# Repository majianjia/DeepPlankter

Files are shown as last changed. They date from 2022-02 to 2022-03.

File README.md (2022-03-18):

# DeepPlankter

An autonomous wave and wind propelled drone boat.

It uses free energy in the surrounding environment to sail for a very long distance. It relies on in-air free-rotate wing and the underwater wings to provide propulsion and solar panels to power the onboard electronics.  

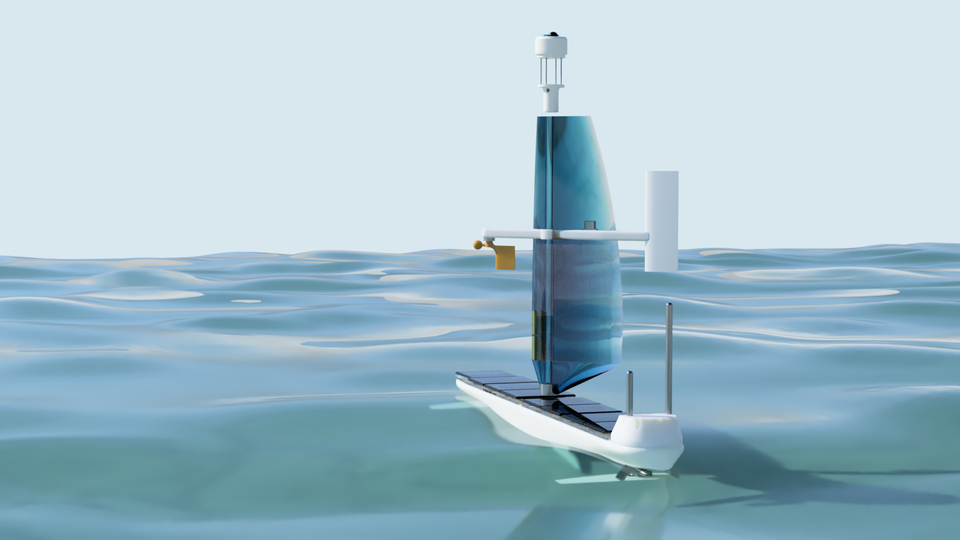
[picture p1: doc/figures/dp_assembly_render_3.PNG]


This repo hosts the main design files (PCB, mechanical parts and development logs) of the DeepPlankter project, excluding the boat controller firmware and communication method.

- The source code of **navigation controller firmware** will be hosted in its own [repo (Not yet public)]() 

- **Communication protocols and the remote control App/Website** are **NOT** opensourced because of safety reasons.

### Building log

1. [Hull building](doc/hull.md)

2. [Underwater Wings](doc/underwater_wing.md)

3. [Navigation algorithm](doc/navigation.md)

4. [Science Payload](doc/science_payload.md)

### Experiment log

1. [First motor powered experiment](doc/exp1_pond.md)

2. [Second motor powered experiment](doc/exp2_pond.md)

# 3D designs

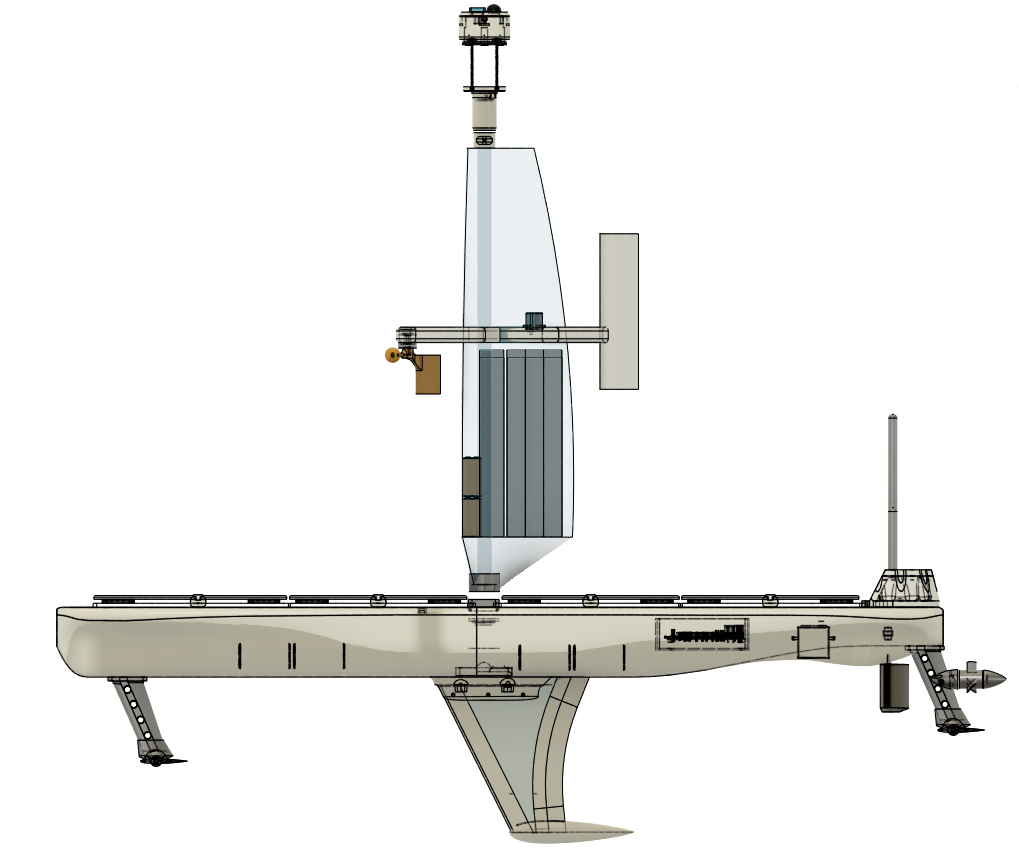
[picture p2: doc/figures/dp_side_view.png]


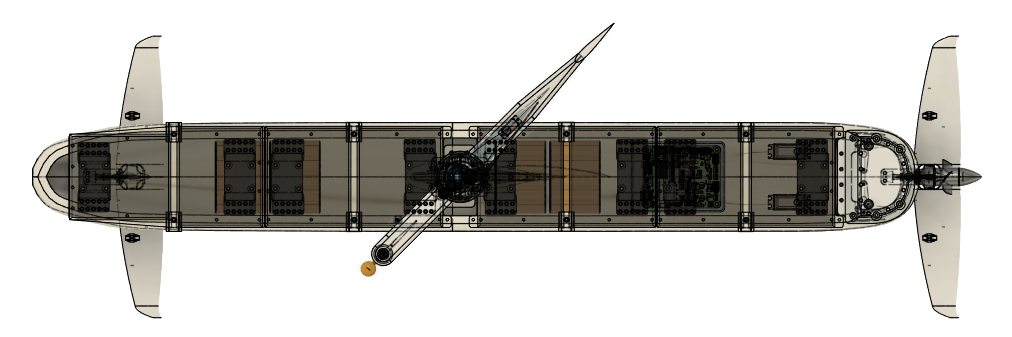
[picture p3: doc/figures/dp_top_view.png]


# Hardware

PCB file can be found in [PCB](PCB) folder. 

**The boat controller:**

- Dimension: 80 x 100 mm
- MCU: STM32H7A3ZI, 280MHz, 1MB SRAM, 2MB Flash. 
- NorFlash
- RTC

**Sensors:**

- IMU: BMI088
- e-compass: HMC5883L
- Environment sensor: BME280 (humidity, atmospheric pressure, temperature)

**Power supplies:**

- DC/DC LMR33640, 5.1V, 4A (max) x 3 controlled channels.
- DC/DC LMR33640, 3.3V, 4A (max) x 2 controlled channels.
- 2 battery connectors 
- 2 charging connectors. 

**Power connector functions and monitoring**

| Connector | Ctrl. Switched | Voltage gauge | Current gauge | Comments |
| --- | --- | --- | --- | --- |
| 3.3V (CH1, CH2) | yes | | | |
| 5V (CH1, CH2, CH3) | yes | | | |
| BAT (CH1, CH2) | *yes | yes | yes | Base on ideal diode controller. |
| Charge (CH1, CH2)  | | *note | yes | Voltage = BAT |
| ESC power | yes | *note | yes | Voltage = BAT |
| Servo (CH1, CH2) | yes | *note | yes | Voltage = BAT |
| Servo (CH3) | | *note | | Voltage = BAT |

**Extension IOs:**

- 2 x 2P NTC (for each battery)
- 1 x 2P ADC
- 1 x 2P External LED (Flash light)
- 1 x 2P External Buzzer
- 3 x 6P UART (marked TELE1, TELE2, main GPS)
- 2 x 4P UART
- 2 x 8P SPI (MISO, MOSI, SCK, CS1, CS2, IO)
- 2 x 4P I2C (same PHY)
- 1 x 4P FDCAN
- 1 x USBD
- 1 x 24P FPC DCMI camera interface (for OV2640)
- 1 x 8P FPC and 2x4 rows debugging port (SWD + UART)
- 1 x SDCard slot (SDIO)

## Battery, solar panels and MPPT chargers

- Battery 1: 18650 1500mAh 2S 9P
- Battery 2: 18650 1500mAh 2S 9P
- Panel set 1: 12V 160mA 4P 
- Panel set 2: 12V 160mA 4P 
- MPPT charger: BQ24650 model x 2
- 2S over current protector and balance x 2
- NTC x 2

The power of the whole boat is purely supplied by solar panels. We need to ensure the main controller never run out of power. The power distribution is managed by the main controller board. 8 panels are grouped into 2 set with 4 panels in each set. Each set of panels charge one battery through an independent MPPT charger and is balanced by an independent protect board. The power from the 2 batteries finally merges to a power rail through 2 ideal diode circuits. Then the power can be distributed by the main controller board.

The voltage and current of each charging circuit and battery are monitored.

### Energy estimation

Each panel is rated 12V@160mA. In a sunny April day noontime, the maximum current measured is 10.5V@120mA when laying flat (simulate the angle on the boat).

So the peak power is around 1.25W for each panel. 8 of them can generate 10W.

But there are efficiency drops due to DC/DC converter and the battery charging efficiency. We assume it is around 0.8, so the peak power to charge the battery is 8W.

The peak power multiple by the term, "peak sun hours", is the energy that generated per day.  
For example,  per [this blog](https://www.pveducation.org/pvcdrom/properties-of-sunlight/average-solar-radiation#), in UK summertime, the peak sum hour is 5 hours, while in the winter, the number drops to 0.5 hours, so the power generated per day is around 40wh to 4wh.

> The average daily solar insolation in units of kWh/m2 per day  is sometimes referred to as "peak sun hours". The term "peak sun hours"  refers to the solar insolation which a particular location would receive if the sun were shining at its maximum value for a certain number of  hours. 

Sailing during the winter is definitely a nightmare for the boat no matter how big the battery is, it will be drained out very soon if we don't cut off the power to every module or put them into sleep mode.

We have 2 battery sets, each can store around 100Wh. It needs 5 sunny days to fully charge.

Both batteries together can supply a 1W consumption (3.3V 300mA) for a good week until the next sunny day. Or 0.2W (3.3V 60mA)for a month.

# Contact

Jianjia Ma 
`majianjia(-at-)live.com`

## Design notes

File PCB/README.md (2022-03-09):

# Hardware Defect

- Console UART debug port tx/rx swapped. 
- Camera LDO 2.8v and 1.2v switched. 
- R90 removed

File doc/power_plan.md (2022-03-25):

# Power plan

The the power all power plan on the boat is shown below.

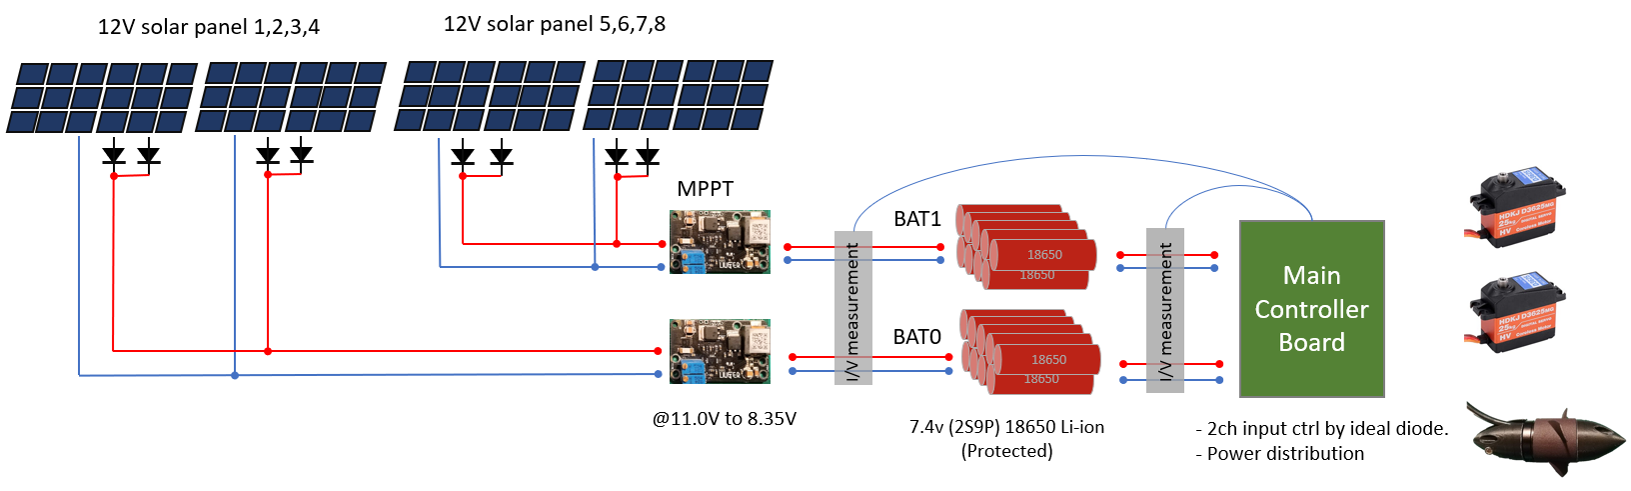
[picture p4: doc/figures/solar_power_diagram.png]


This is a simplified diagram that doesn't include power switches, battery protection circuits, temperature sensing and some other current sensing. 

## Solar panels

Our panels are laid flat on the deck so the sun angle is very important for the test because the angle of light affect the effective area on the panels. 

The panel has rated 12V at 160mA under 1000W/m^2 (this number is about the direct sunlight on the ground). According to my previous measurement, each panel measured open-circuit voltage at 13.7V and short-circuit current at ~150mA. 

A solar panel power test was done on 17 March.

On 17 March 2022, the maximum sun angle is 40 degrees in Southampton UK. If we only consider the power is produced by the direct sunlight but not scattering light (discuss later), the panels generate 76% power of its right angle sunlight theoretically.

As you can see from the power plan diagram, we have 2 sets of panels, 4 panels per set. Each rated 1.8 W according to their official data. So the maximum output for use should be 1.8 x 76% = 1.35W. Below is the measured power from the 2 sets of panels. 

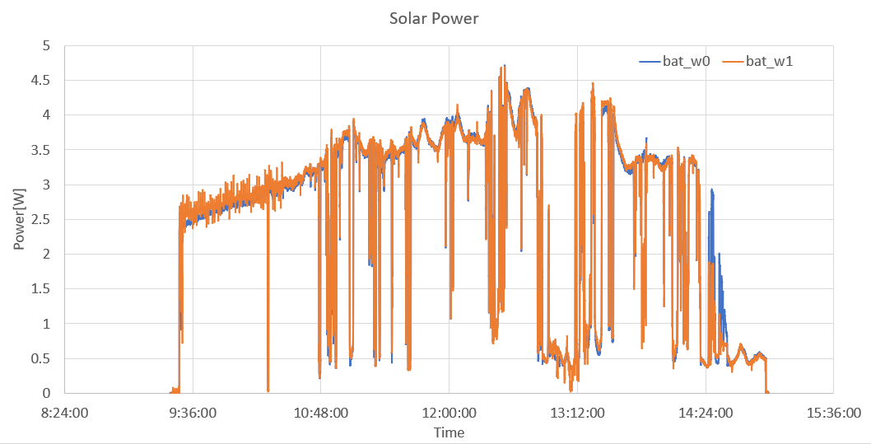
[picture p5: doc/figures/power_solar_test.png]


There is some noticeable information from the graph. 

- Both sets of panels generate very similar output.

- At peak sun degree (12 o'clock, 40 deg height), each set of panel generate 4W power, (1W per panel), this number is lower than our calculation of 1.35 W. There are multiple reasons for it, 1) the series connected Schottky diodes consume power. 2) the MPPT voltage is set lower than the optimal voltage (discuss later.) 

- The peak power isn't the clear sky. If you see from 9:30 to 10:30 when the sky is crystal clear, the power output is steadily increased, but starts around 10:48, a higher peak power is received but together with some drops. The drops were due to cloud shade. The increased peak power is because the cloud is scattering sunlight which leads to more energy radiating on the panels. This is only my thought to explain this counterintuitive phenomenon. Whether the at a certain density of cloud will generate more energy than clear sky, I don't know. 

- In total, during the 5 hours experiment, the 2 sets of panels generate 24Wh energy, if we expend the time before 9:00 and after 15:00, I estimate it can generate 36Wh. I think this result is very promising. One of these partially cloudy days allows the boat to work 2 to 3 days. I am sure the boat can sustain most of the year and bad weather. 

What this number also means is that the sunlight can drive the boat in the daytime infinitely with 20% of the thruster throttle. In the second motor-driven test, at 20% throttle, the motor takes around 6W power while it can push the boat at a speed of 1.5 knots.   

Below photo was took at 10:26. 

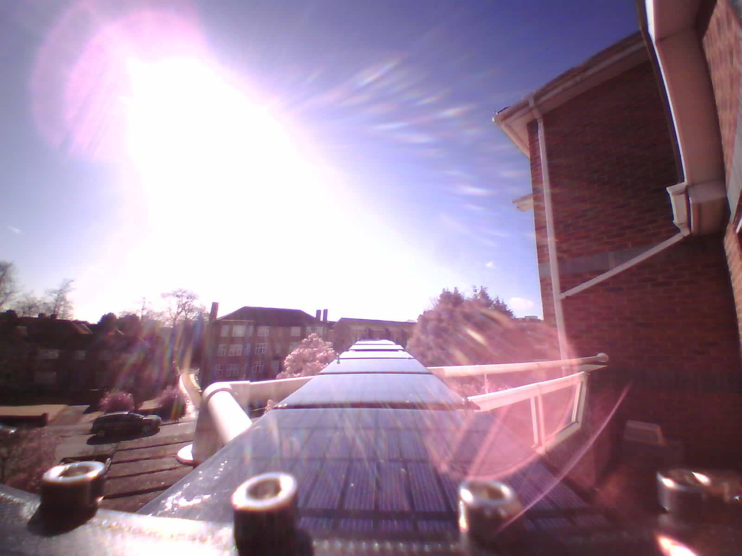
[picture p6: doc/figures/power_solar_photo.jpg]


## MPPT voltage and charge voltage

The MPPT module has 4A maximum current but apparently we won't use that much. The nominal voltage for the solar panel is 12V (24 small cells in series), but because we are using parallel connections, a Schottky diode is needed for each panels, in case of uneven lighting causing too much reverse current (turning the shaded panel into LED). Because the voltage drop of the diode, the MPPT point should be set lower. Per the datasheet of the diode I used, the voltage drop at 100mA is around 0.4V. So the MPPT point should be tuned at 11.6V. 

However, if you see the graph carefully, you will notice that the MPPT
voltage is in fact set to 11V which is lower than our calculation above. My
consideration is

- When the lighting is low, the solar panel's MPPT voltage is also reduced. If we still use the higher voltage, we will get very little power out. This is very important because we want the panel to produce power in bad weather more than on sunny days. A lower MPPT voltage decreases the power output on sunny day a bit but will ensure the panels work in darker lighting conditions.

- Besides lighting, a lower voltage can ensure all panels has space to generate current when they are not exactly the same. For example, some of them might be degraded differently during a time or they came with manufacturing defects. Result in cannot reach the higher MPPT voltage.

- Since we have a fixed MPPT voltage setting, a lower voltage will ensure us a larger safety margin.

To be continued..

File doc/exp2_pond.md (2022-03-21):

# Second motor powered experiment

After the first experiment, lots of issues were found. Fixing them took quite a lot of time but finally was all solved. .

So I decided to take another motor propelled experiment to test the rudder effectiveness and the waypoint mission. 

Overall, the experiment went well. 

- rudder effectiveness improved by increasing the angle limitation and extending the length. 

- There is still a problem with LORA communication. 

- There is only one water leaking issue found on the bow deck due to a unscrew bolt. 

- Waypoint planning seems effective, the boat can drive itself toward the waypoint and path direction. Although the turning radius is still quite large. 

- Camera exposure is now working correctly, however, there were some issues with the wire connection. All images taken during the experiment are broken, cannot be fixed. It's a pity. 

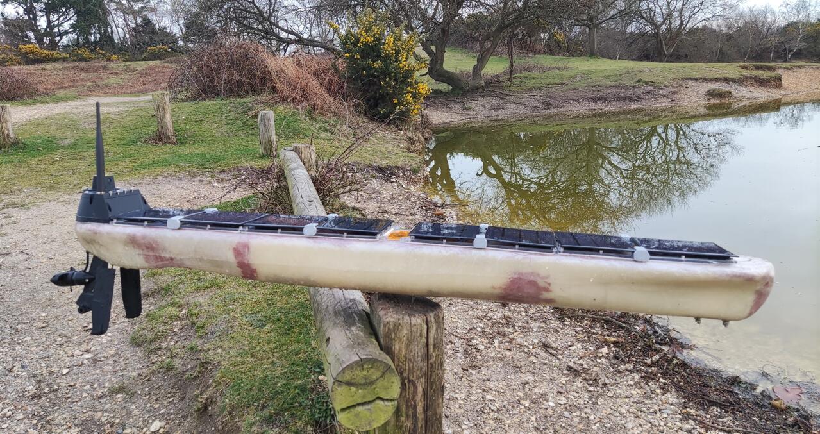
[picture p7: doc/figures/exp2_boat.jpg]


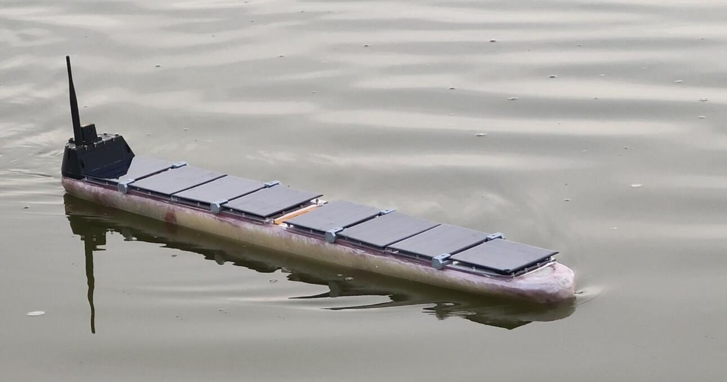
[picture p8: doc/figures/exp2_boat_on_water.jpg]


## Waypoint mission

Thanks to the navigation simulator, I was able to validate my navigation algorithms in the simulated world. See the [navigation development log](navigation.md) for details.

I use the default parameters for the waypoint mission, which is very rough and conservative. however, it did work well. The PID parameters were set to 1, 0, 0. which means every metre of  *cross track error* turns the rudder for 1 degree. No integration and damping components. The pond seems a little bit small for testing the waypoint function but the result is still exciting. 



While we solved the EMI issue, the GNSS can locate the boat pretty well now. 

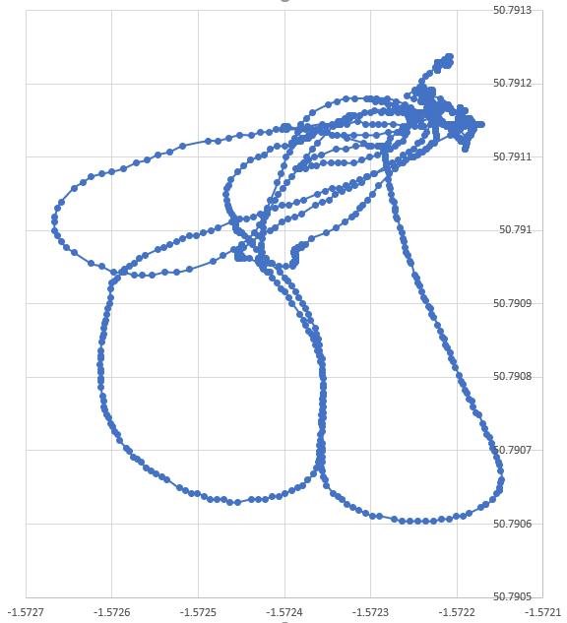
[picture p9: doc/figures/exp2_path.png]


With only 20% of throttle, the boat sails peacefully. 



## Unstable rolling motion

without hydro wings, keel and underwater ballast, the boat is still unstable at high throttle. 

I am not worrying too much about that because when the wing sail is ready, we must install the keel together with the ballast. 

## Minor water leaking

The gaps between the screw and polycarbonate glass are not sealed correctly. When water came up to the deck, it is leaking into the boat. I bought a bag of O ring for sealing the gap, hopefully can fixed this issue. 

The other water leaking source is the screws for the 3D printed solar panel mounts. The bot underneath became loose very easily when some water is leaking in. I would seal them with silicone glue for the future test.

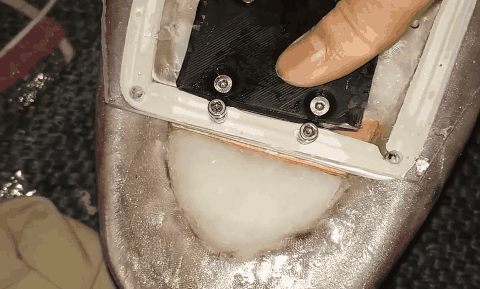
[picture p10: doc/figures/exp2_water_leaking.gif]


## Batteries management issue

- One of the protectors is broken. Looks like the IC is bricked at charge protection. I could not recover from the error state. I replaced the protection board with a working one.

- The motor drain majority of current from one of the battery. Later found this was due to a short under the ideal diode controller.  Fixed. 

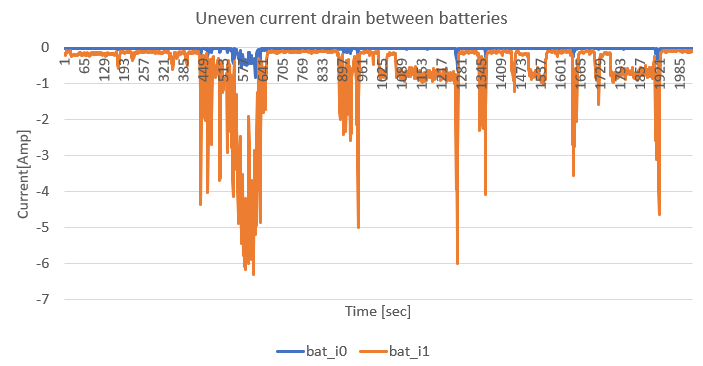
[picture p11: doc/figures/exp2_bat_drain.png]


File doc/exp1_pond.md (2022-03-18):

# First motor powered experiment

Did a experiment at Setley Pond, New Forest this Sunday afternoon 7th March 2022. 

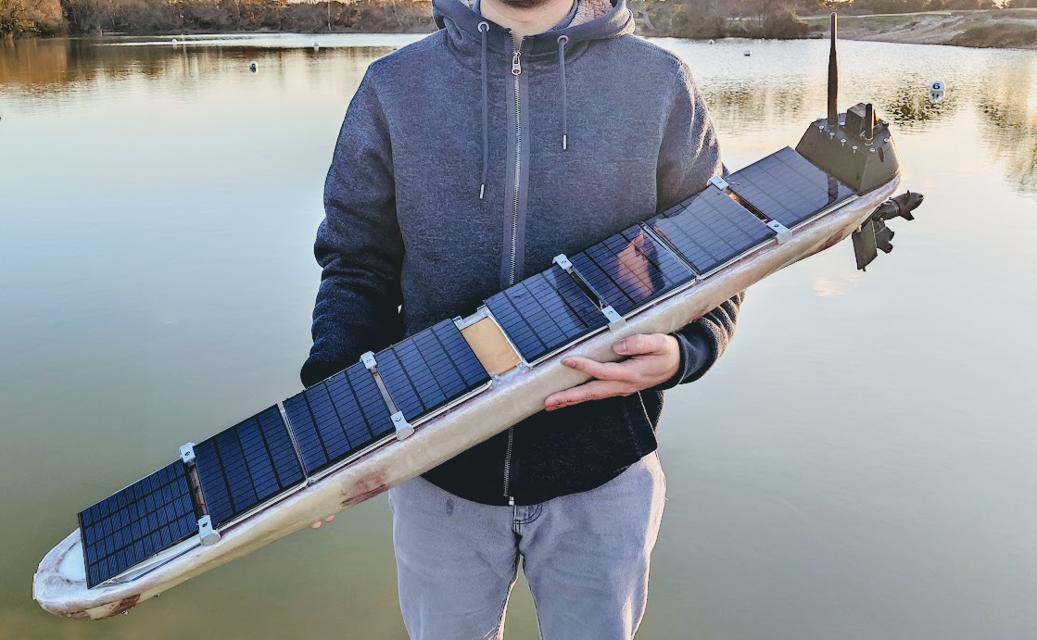
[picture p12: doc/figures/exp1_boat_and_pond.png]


In this experiment, I would test a few different things. Including

- manual control and motor drive.
- underwater wings. (cancelled, due to no wave)
- waypoint mission. (cancelled, due to low rudder effectiveness)

As you expected, this experiment wasn't going well. Fortunately, the boat float and recovered. Also, [data](../experiments/2022-03-06%20dp%20first%20water%20run) are recorded so we have something to analysis.

The motor can really push the quite fast, even the throttle has been limited to 50%. The motor consume around 5 Amp current at 50% throttle. When I pushed the throttle fully from the App (50%), I am quite worry about the boat sinking into the water and become a submarine... Beside the boat was not being able to turn, it is really fun to play with.



Trying to plot the GNSS location in a map, but due to the EMC problem that discuss below, the GNSS can only be located by 4-5 satellites during the trial, the accuracy is pretty low, the path is meaningless. 

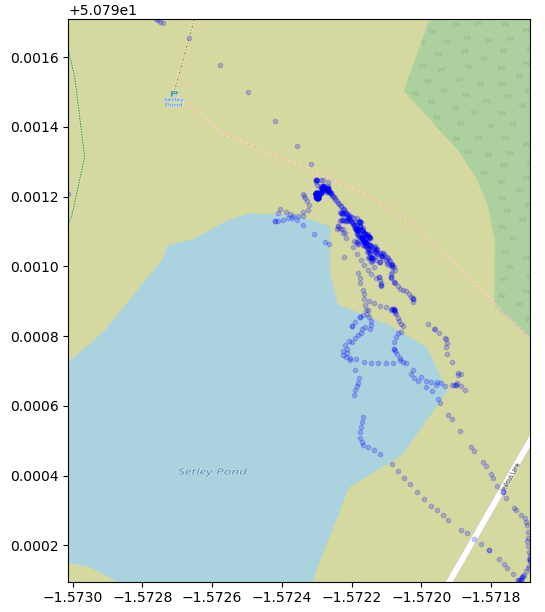
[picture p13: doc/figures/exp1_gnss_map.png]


In the next sessions, I will show the issues that found during the experiment and some of the solutions. 

## Issues

- [EMC problem with antennas](#emc-issue). 

- [Water leaking from unknow source](#water-leaking-issue).

- [Dead servo might due to over voltage](#servo-found-dead).

- [Low rudder effectiveness](#low-rudder-effectiveness). 

- [ESC response too slow](#esc-response-too-slow). 

- [Batteries magnet field affecting magnetometer](#batteries-magnet-field-affecting-magnetometer). 

- [Boat mass centre too high, unstable](#boat-mass-centre-too-high). 

- [Camera data error and image over exposure](#camera-data-error-and-image-over-exposure). 

### EMC issue

At the experiment, all antennas are placed in the bridge at the tail of the boat. 

SIM800C's antenna is placed closed to LoRa's antenna, even in  the same direction. What makes things even worst is they are working at a similar frequency band 800/900M for GSM and 868M for LoRa.  It was ok during home test because the city area has better cellular coverage so the GSM module won't emit too much power. But in the rural, it starts to emit more power so the LoRa is now struggling to send/receive data. 

GPS module also suffered from the GSM module's RF. From the data it recorded, I can see there is only 5 satellites connections when the boat was on the surface of the water, where the signal is weaker. But when I recovered the boat and raised the boat to my car's boot, then it can see 10+ satellites.

The potential solution is to move the GSM module and its antenna to the bow of the boat. 

For the Iridium, I think it will be ok to stay at the tail bridge because it won't be activated too much. 

The GSM module cannot be placed at the mat because the QingStation uses BME280 for pressure and humidity measurement, which is RF sensitive. 

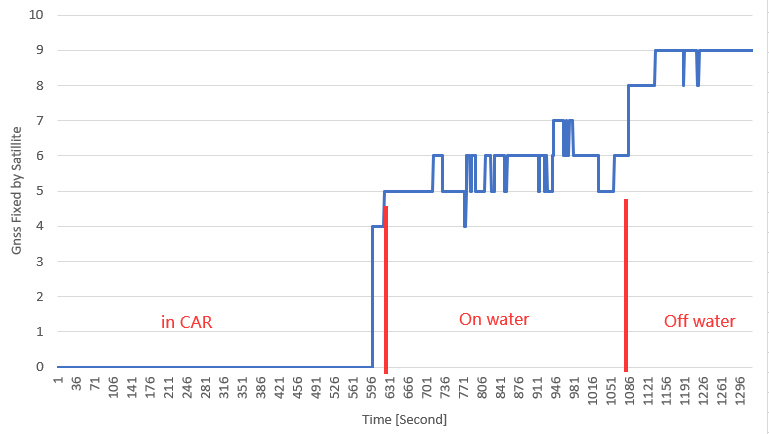
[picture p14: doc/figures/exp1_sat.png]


### Water leaking issue

There was a half cup of water found after I returned home. It is fortunate that I remove the battery from the controller board before I set off. I had to dry out the batteries because they are wet. 

I think it might come from some screw holes that I did not put a screw in. Hopefully, I can fix that later. 

### Servo found dead

One of the servo, servo 1, left rudder, was found dead just before deploying the boat. I supply direct battery voltage to the servo, which is 8V currently, the Servo's working voltage was rated at 4.8 to 7.2V. Looks like it burned out the servo. I disassembled the dead servo but couldn't find a burning spot on the controlling PCB. The reason of the failure remains unclear. 

I order a few mini-360 step-down DC/DC boards to lower the voltage and a new servo to replace the dead one. I would set the voltage to 5.5V. The recorded peak working current for these servos is less than 1A. I believe the small DCDC board can handle the servo's current.

### Low rudder effectiveness

This issue is partially related to the dead servo, but also the length of the rudder is underestimated. I did try to build an extended rudder that can stick on the existing rudder which I brought long time ago designed for RC boat. 

The range of servo is set to +-30 degree, which seems too narrow. It is now increased to +-60. The actual angle that the rudder can turn is smaller than servo angle. 

With only one working rudder, the boat can barely turn at high speed. I think that is because the motor was placed far behind the rudder.  The blue highlighted part is the new extension that will be added to the rudder. 

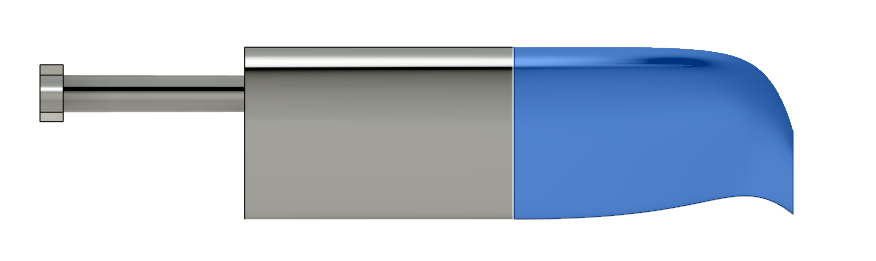
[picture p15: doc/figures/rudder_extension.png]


### ESC response too slow

I added a smooth throttle response in the software to eliminate the immediate change direction of the motor. But the value is too large. Adding some signalling delay, the boat feels like out of control many times, did not response for 5 seconds, while I did hear the servo is still responding to my command. Easy fixed issue. 

### Batteries magnet field affecting magnetometer

Fixed by moving the battery forward.. 10 cm away of controller box.

### Boat mass centre too high

Due to the heavy solar panels, the decks and the screws to fixed the decks, the mass centre were lifted too high, resulting in unstable roll motions. Even the propeller rotation cause 20 degrees rolling. 

I brought 1.8kg lead ingots for ballast, each 450g. I will attach 900g to the bottom of the boat hull. When the keel is ready, I will then move them to the bottom of the keel for the best ballast. 

### Camera data error and image over exposure

Due to the low-frequency clock, 2.5MHz, while the OV2640 require at least 6MHz. The OV2640 seems cannot automatically adjust the exposure time (not short enough). The signal length is too long, about 30CM, any clock higher than 2.5M will not work. It is already producing quite a lot of byte error at 2.5M, see images below. 

I will turn the software while keeping the frequency low. If there is no way to configure it, I will try to attach a grey scale filter on the lens to lower the lights. 

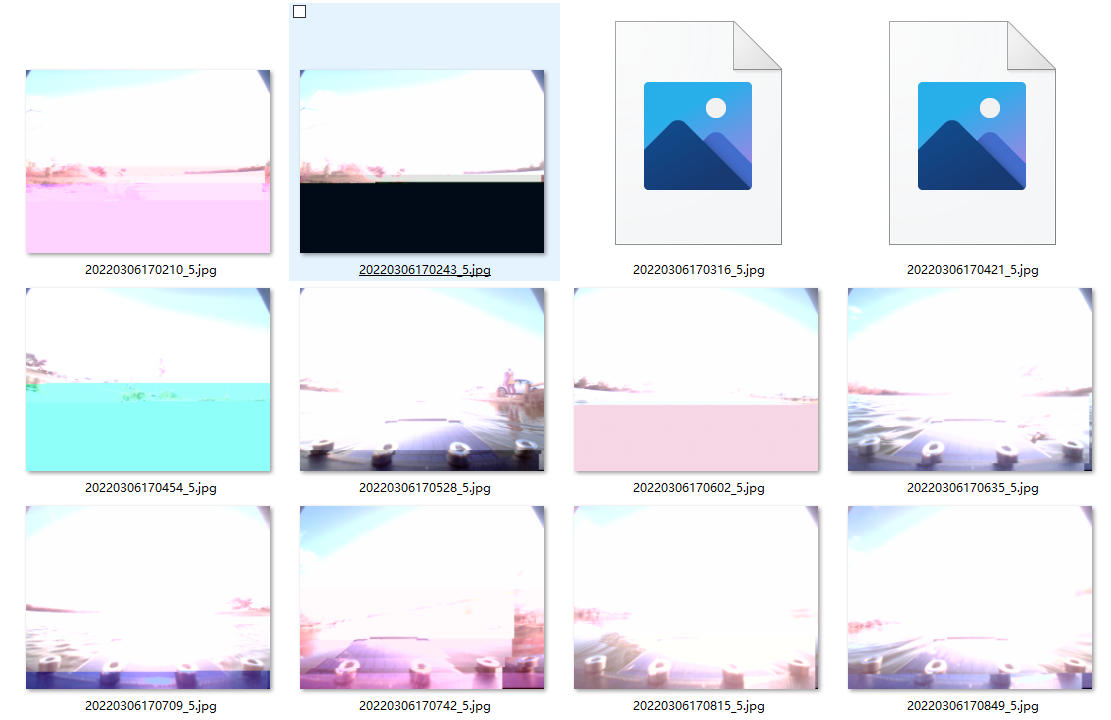
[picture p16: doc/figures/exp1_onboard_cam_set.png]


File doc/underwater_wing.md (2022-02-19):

# Underwater Wings

The underwater wings are to convert the vertical motion (wave) of the hull to small forward propulsion. So the boat can sail forward without the need for energy.

I was planned to build the wing core from wood pieces. Cut the shape, then sand it down to streamline. But later I decided to let the 3d printer build the core. There are some issues with 3d printed parts.

- The PLA materials that 3d printer used might degrade in salt water ( which is not, later confirmed by research paper. )

- PLA can crack easily. 

- If we reinforce with glassfibre and epoxy, the epoxy has difficulty to glue on epoxy. 

To solve the second problem, we use a tough PLA to print the main part. For the third problem, I planned to use rough sand paper to sand it down and leave more scratches for the epoxy to grab on. 

I didn't use a standard airfoil on the underwater wing but built from my own experience from RC planes. The airfoil is symmetric so it should perform the same for both upward and downward directions.  It also has a small wing tip to lower the drag from induced drag (not sure whether this is useful but looks cool. )

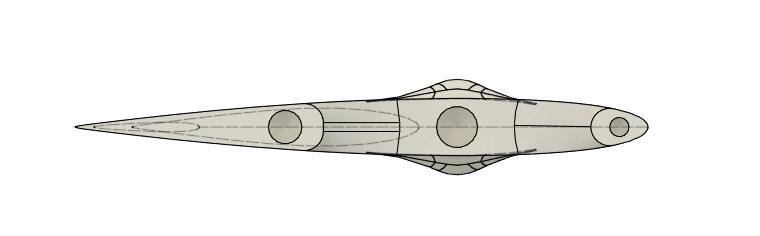
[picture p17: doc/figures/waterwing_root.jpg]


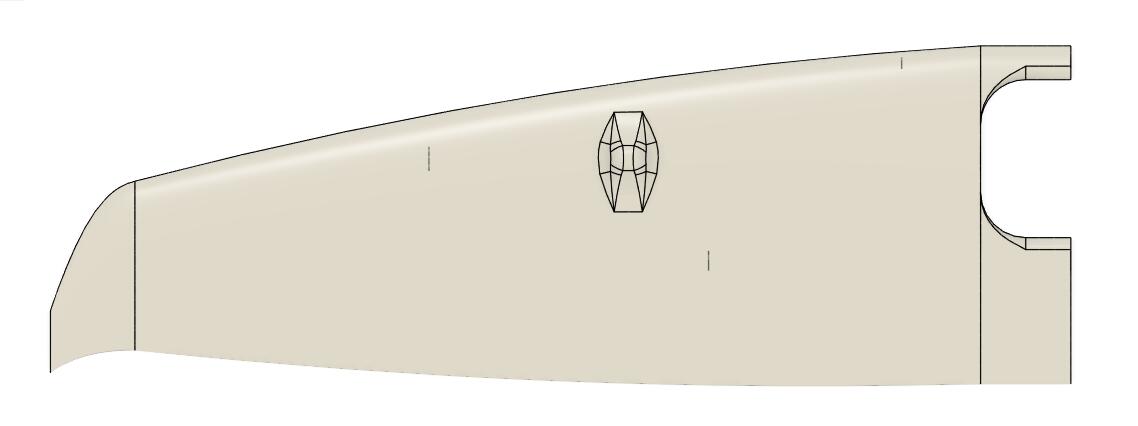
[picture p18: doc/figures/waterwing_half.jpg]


Underwater wings are normally spring-loaded so the wing can work efficiently during different vertical motions.  [This paper by University of Southampton](https://eprints.soton.ac.uk/442253/1/Forward_Speed_Prediction_of_a_Free_Running_Wave_Propelled_Boat.pdf) has thoroughly investigated the speed and different underwater setup. 

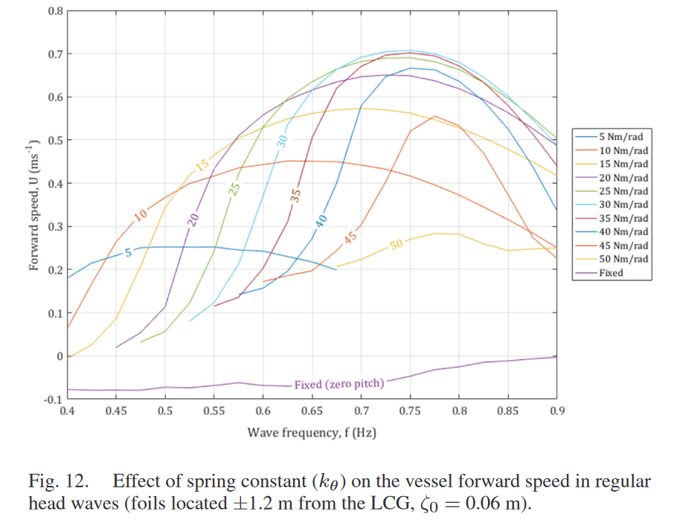
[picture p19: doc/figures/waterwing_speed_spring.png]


Although, high springs loaded wing will produce faster speed when the wave frequency match the wing design. Load springs load has a much wider working range. However, the above data are from their testing design, in which wing has a larger chord (see the original paper for details).  

I don't plan to use springs on the wings. It is hard to match springs. Also, I don't think it is necessary since our wing has a short chord, so it should turn to its maximum positive or negative angel very quickly where propulsion is generated. 

If this doesn't work well, I will consider adding springs. 

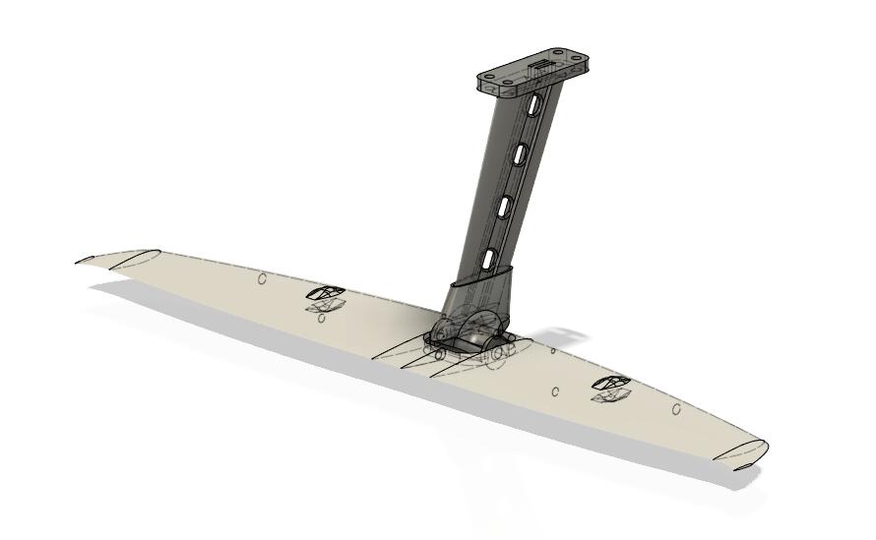
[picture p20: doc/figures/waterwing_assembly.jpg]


Today, the wings core are printed. 

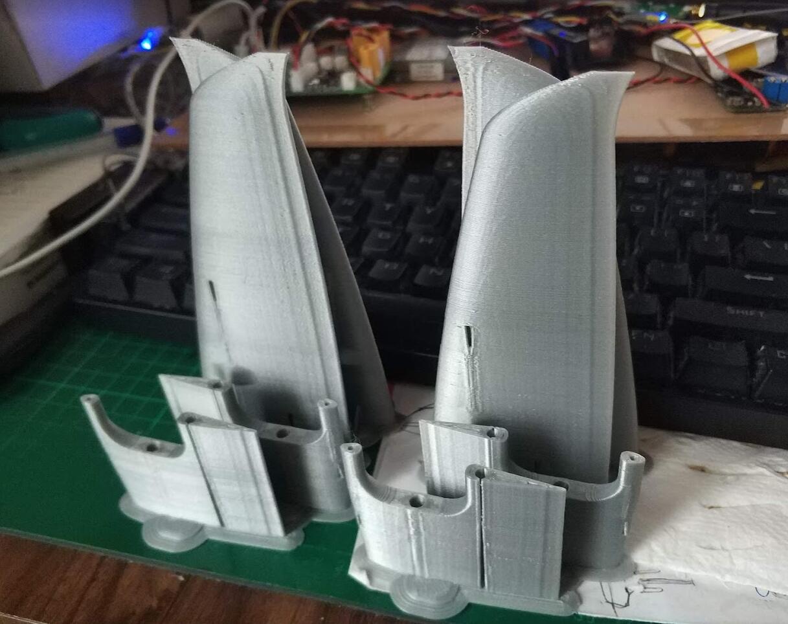
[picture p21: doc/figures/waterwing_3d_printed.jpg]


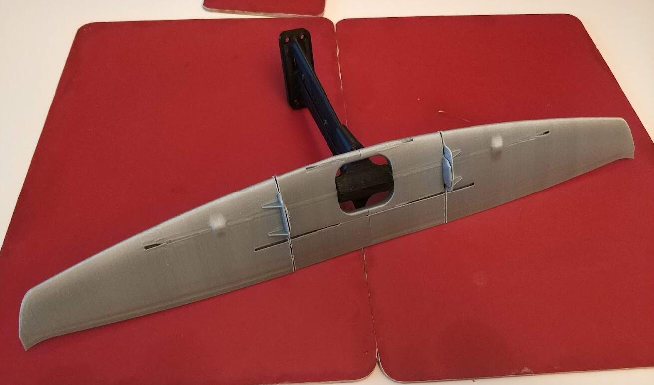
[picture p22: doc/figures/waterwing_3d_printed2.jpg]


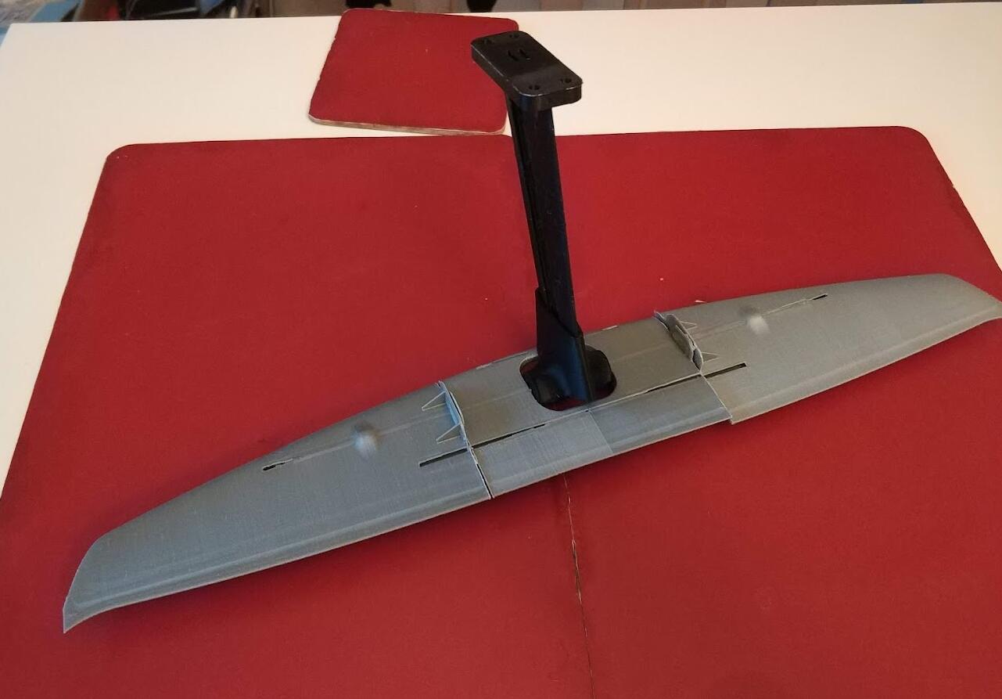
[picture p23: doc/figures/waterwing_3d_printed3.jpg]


A 4 mm stainless steel axis is used. All weight and lift are loaded on the axis. This is where the wing will rotate on. This location is at the ahead of the lift centre, so the wing  will lead to the vertical movement and covert the lift to the forward force. 

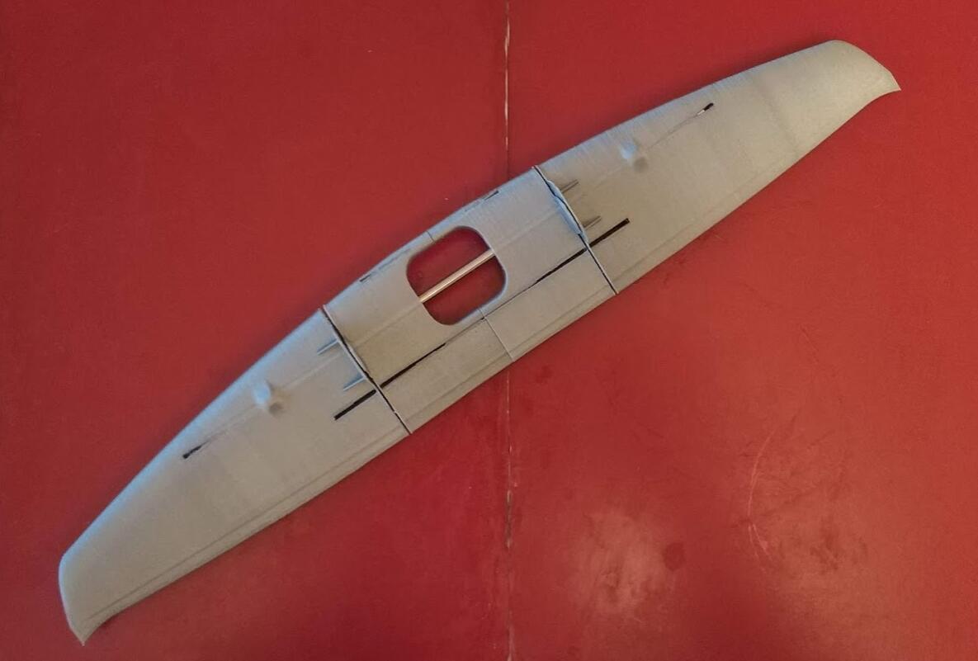
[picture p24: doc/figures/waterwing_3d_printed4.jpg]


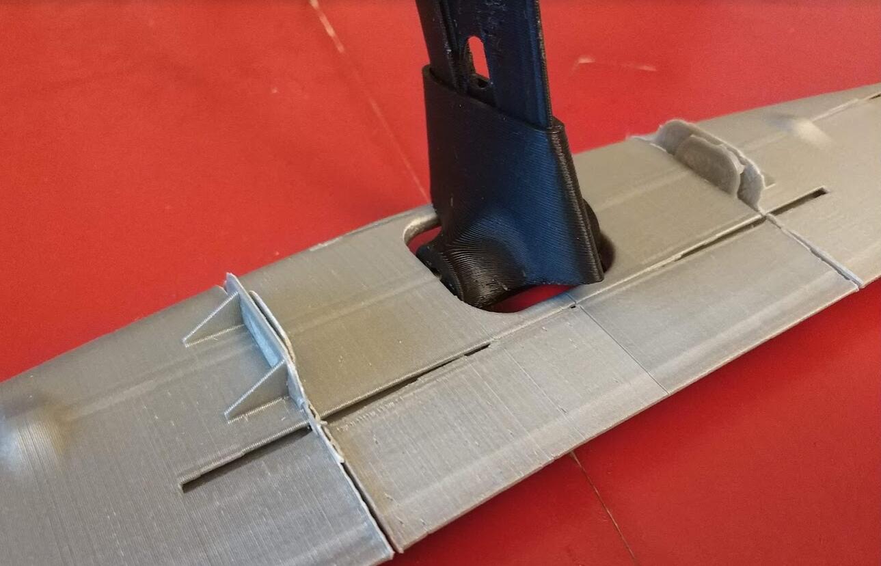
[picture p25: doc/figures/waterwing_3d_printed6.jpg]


The next step is to glassfibre this wing and the supported mount. 

To be continued.

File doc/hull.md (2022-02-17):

# Hull building

I have almost zero experience in designing neither building a boat hull. During the building, I made quite a few mistakes. But finally, something was built...

## Hull designing

There are some points that need to take care of when designing the hull. 

- The hull should be as skinny as possible. To lower the drag, also allow my 3D printer to print the segment (<18cm diameter).  
- However, the deck area should be large enough to hold as many solar panels as possible.

A smaller boat requires fewer materials to build, which will always lower the cost. So I basically designed the deck that can host the minimum number of required solar panels. A single panel size 11 x 13cm, generate a peak power of 2W. Per the preliminary calculation, we will need at least 8 of them. 

Since the boat will sail at a lower speed (< 2knots), a small displacement hull is enough. Here is the design.

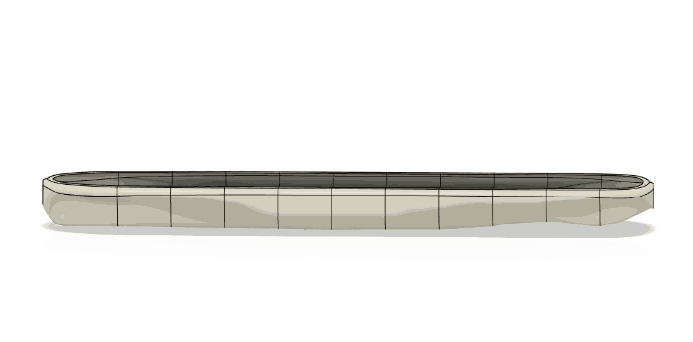
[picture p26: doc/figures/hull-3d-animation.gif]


- Total buoyancy: ~15kg

- Displacement: ~8kg

- Length: 1140mm

- Width: 140mm

- Height: 90mm

The hull has almost the same 140mm width for 90% of the length. Allows the panels to lay on most of the deck evenly. The front of the hull underwater part is a typical displacement hull design. I didn't pursue a narrow tip which is normally used in high-speed hull or RC model sailing boats. Because we still need a large top for the panels and the boat is too small which will easily be submerged in the incoming wave.

Also, the large top also increases the buoyancy when submerged in a wave. This increase the instability in a normal boat hull, which is not a good choice. However, with wave propelled wings, the increased tip buoyancy will lead to more lift on the front underwater wings. Thus, it should provide more propulsion. The lift loaded on the wing stabilized the boat.

The tail design also follows a similar principle of steep buoyancy change, with the bottom of the hull (at the end) being raised near the waterline. When a wave comes, the buoyancy will increase very quickly to pull up the tail underwater wing.
At the tail, there was also a motor mount and the hull stick out for protecting the motor. But later found this is not a good design.

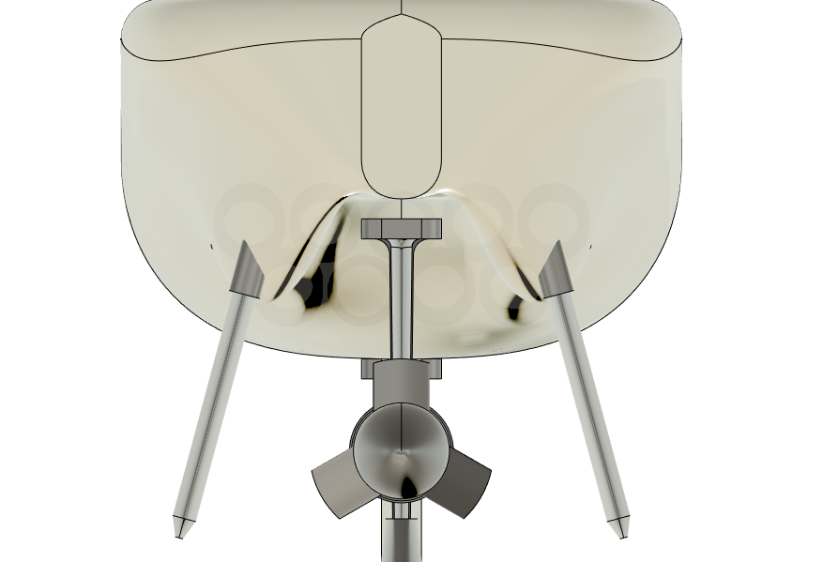
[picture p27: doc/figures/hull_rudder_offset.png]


We will have 2 rudders (for backup). Rudders are offset to the side by 15 degrees. It was meant for better steering during sailing. When the wind hit the air wing, the lift of the air wing will not only generate propulsion but also a side force (actually, the side force will be larger than propulsion most of the time). The side force will cause the boat to roll quite much. The offset rudder will be more effective compared to the regular rudder.

## Hull building

After some search online, I decided to build the hull with epoxy and fibreglass. So I brought some 300gsm fibre chopped strands, 300 gsm cloth and 1kg epoxy.

I don't want to build a mould because it is too complex for me to do. I decided to print the hull using my 3D printer, then glue them together. Then apply a 3mm fibreglass-epoxy on the outside. Then sand down the surface to make it smooth.

The plan sounds ok but ends up with a lot of trouble!

- First, the fibreglass chopped strands and cloth are too rough for a small boat like this. They cannot easily band during the corners. I have to keep bending it during the final curing hours. But the result is still not perfect. It also result in quite a lot of bubbles after I remove the 3D printing part. It might result in leaking water!

- Second, the epoxy is refused to glue on my 3D-Printing materials (PLA+). The connection is not strong enough. PLA can be torn off into large pieces.

- Third, the surface is not perfectly smooth. Epoxy did a great job for self-smoothing but the cloth is too rough, making it impossible to sand down. I have to buy another roll of 100 gsm fibreglass cloth to do a final layer and a coating epoxy layer.

Fortunately, the structure are firm enough. I can even stand on the hull. The final coating also filled in the small bubbles. 

### 3D Printing

Printing the bow section



There is a big hold on the bow. It is expected and ok since we will cover it with epoxy and fibreglass. 



Fixed bow



Glued hull. The shape is already there. The quality is quite good. There is no twisting which I was quite worried about. This bench will also be my main working station for the rest of the building.



The next step is fibreglass the outside of the 3D printed hull. The first layer is chopped strands. 



Last layer use fibreglass cloth. It looks all right but the deck is already starting to tear off by gravity and the tension of the cloth.



After it was cured (and being exposed to the weather for a few months...), I then sand it down the first time, leaving quite a lot of hollowness. So I brought some "microballoons" as filler. But when I receive the package, I found it is dark colour which was not expected. I did use it once before on my RC glider, it should be bright white colour. Later I found out this microballoons is not glass balloons but some plastic.



Mixing the micrballoons with epoxy.



The colour was really not pleased, at least not my favour. 



When the filer is cured, I sand it down and apply another layer of 100gsm fibreglass cloth. 



Then I remove most of the 3D printing parts from the inside because they are too easy to be a breakdown, I couldn't rely on fixing parts on the 3D printed part but have to directly contact the epoxy part.

After the final layer, I sand them down and a final coating. It is quite smooth.



The fibre epoxy part is now finished. I then reinforce the wooden board for use as a deck.



They are then being glued inside of the hull, with direct contact to the epoxy for maximum strength. Below is the middle deck, which will also hold the mast so I use a wider board. I also cut some cross lines to enforce the contract. I did not add a layer of fibreglass here. Hopefully, it is strong enough. 



Another layer of epoxy coating for water-proofing. 



By now, the hull weight 1.7kg.

There still many works to do, such as foam filling, drilling and painting. They need to be done after electronics/actuators are installed. 

To be continue..

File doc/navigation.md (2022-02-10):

# Navigation

Navigation is a challenge for a small boat like
DeepPlankter.

- The ship might equip with a free-rotated wing. Headwind and tailwind will generate little-to-no force. The boat needs to offset to the wind direction.
- The propulsion (from wing or wave) is small and unstable. It can even be pushed back by wind or sea current. The navigation should be able to drive the boat back in this situation.  
- The boat cruising speed is very low.  

## Simulator

> The source code is available in the dedicated [navi-sim repo](https://github.com/majianjia/nav-sim)

To ensure the navigation algorithm works as expected, I actually build a 2-D simulator out of [Processing 3](https://processing.org/). Processing 3 is basically a java graphical lib with some customized interfaces. This simulator is extremely helpful for me to develop a navigation algorithm. 

Up until today, it has the features below:

- Ture earth coordination
- Dynamic wind simulation [direction, wind guest, wind speed]
- Dynamic sea current [direction, speed]
- Drag
- Boat physical model
- Interactive waypoint 
- Time wrapping

Although most of them are very simple, they still can cover the most extreme situations such as strong wind, guest wind and strong current.  



## Navigation strategy

Different drone navigations algorithm have been widely implemented on many open source flight controllers. Actually, most of the opensource flight controllers use the so-called [L1 navigation algorithm (original paper)](http://redmine.roboime.com.br/attachments/download_inline/351/gnc_park_deyst_how%5B1%5D.pdf) or its variances. It is robust and has already been validated by a lot of experienced users.

The most significant principle for L1 is it uses the term "the acceleration back to track" (a_s_cmd) as the key parameter to control the course correction. Also, in many L1 implementations, they assume that η is a very small number so sine can be replaced by linear functions. L1 give drones a very good track following method no matter the track is a line or a curve. It is also very simple to tune because there is only one parameter called L1, which define many things. Such as the track width, the damper for the stay on track acceleration, the length of line-of-sign to track, and others. Here is the L1 principle (figure copyright belong to the paper author).



The question for me is whether I should implement L1 or develop a specific algorithm for the boat. There are some considerations:

- Compared to air drones or rovers, the boat I built is aimed to low speed ( < 2knots) but also at very large scale waypoints (10-100km). The "stay in track" capability is not very helpful since the track can be very wide(100m or ~km). 

- The navigation should also implement the zigzagging algorithm when the boat is heading into the wind direction or away from the wind direction. Otherwise, the air wing give us little to no propulsion or even drag.  

- The boat will also likely be in extreme situations such as strong wind and current in a storm. It is not clear whether the L1 can handle that. (not sure my algorithm can either)

- L1 use only one parameter to define many terms that are used in the algorithm. This is not very feasible for this boat navigation situation.

To sum up, using L1 here will not be ideal, since we are not taking advantage of the following track or the simplified parameter setting. Instead, we still need to have finer tuning parameters such as track width and others. 

We are more interested in large scale direction, for example, the path width can be 100 metres or ~km when in the ocean. Compared to these distances, the boat speed or accelerations seem very small. It is unnecessary to wake up the actuators to do a small correction. We only care about whether the boat is heading toward the right direction in a long time scale (minutes or hours.)   

## Track following

However, track following is still needed, as the distance between the waypoints can be too long, simply heading to the target waypoint will have very limited resistance to interference such as wind and current. What we don't want is not try too hard to get back to the track, which consumes our limited battery power. For the track following, unlike L1, I use a P controller on the cross track distance to get the course correction back to track. This correction is also limited by a fixed threshold, called max_offset_angle, this is normally in range of 45 deg to 70 deg.



This is a very simple P controller, but the P setting will be very low so I am not too worried about oscillation. In the actuator output implementation, there are also heavy filtering and lazy responding implementation, so a small correction will not trigger the servo action (servo will be power down most of the time to save power). 

## Out of track detection and secondary track

Out of track detection calculate the track distance to the primary track. If the distance is larger than n=3 times of track width. The boat will no longer sail follows the track to the primary target. Instead, it creates a secondary target waypoint on the primary track. Then it starts to follow the secondary track to get back into the primary track. 

This seems unnecessary because the track following always drive the boat back to track. However, it is very useful for wing sailing which we will discuss in the next section.  



The insertion point (the secondary target) between the secondary track and the primary track is defined by the boat's current location and the max_off_angle, the angle is set to < 90deg. At least, it will not go backward.

Simulation :



To be noticed that we use heading instead of course for this calculation for simplicity. It is expected strong current will push the  boat out of track quite often. But as I mention, we are not aiming for an extreme track following. 

Also, the parameters we use do not contain derivative components (speed or acceleration), but we assume they are very small values compared to the waypoints and distance which hopefully make the parameters tuning cover most of the case. So, we don't need to do filtering because derivatives can be very noisy. 

## Navigation with air-wing

We know that sailboat cannot sail directly into the wind, there is an angle threshold where the wind propulsion drop dramatically, when the wind direction changes from side to the headwind. Sailors call this no-sail zone. 



For free-rotate wing sail, there will be another zone for tailwind. 

Many researches have been done with wing sailing, such as [Design of a free-rotating wing sail for an autonomous sailboat by CLAES TRETOW](https://www.diva-portal.org/smash/get/diva2:1145351/FULLTEXT01.pdf).  Below is the polar diagram from the thesis. 



This graph represents the wind direction (relative) vs boat speed. It is symmetric for the left and right sides. Here we only discuss the wind from the right. We can see that the boat start to struggle when the wind direction is over 150 deg (tail wind) or less than 30 deg (headwind).

I assume our boat has a similar diagram, so our navigation has to be able to void sailing into these "no-sail" zone. When the course to the target waypoint is close to the wind direction, we need to sail in a zigzag pattern to approach while avoiding sailing into the zone.



I considered the below ways to implement the zigzag path.

- Add temporary waypoints to form zigzag path + strict track following (such as L1). 

- Allow some free sailing zone within a large track. 

For the first method, adding temporary waypoints requires extra calculation and waypoint management. Also, it is not responsive when the wind direction changes during the temporary path. When generating a temporary waypoint, require stable wind direction measurement. This method requires many measurements which will increase the complexity.

For the second method, as I mentioned in the above sections, our navigation method has a large track width. So as long as the boat is on the track, it is free for the zigzag method to decide where to head. The zigzag method can decide the heading freely according to the current wind direction and wing angle. This method decoupled the zigzag algorism with navigation algorism. which make it easier to design.

The below diagram shows the second method. When the boat is within the track, it can sail freely in any direction, and of course, the zigzag algorism will navi the boat following the edge of the "no-sail" zone. When the boat finally reaches the boundary of the track, the track following algorism will override the zigzag output and turn the boat back into the track immediately.



There is a path shrinking angle that will shrink the path near the waypoint. This angle is normally set to arctan(2). 

In this zigzag mode, the "no-sail" zone is dynamically updated, depending on the wind angle measurement (which is relatively reliable). It is very good because the "wind direction" that we use is the relative direction, which combines the boat motion and the real wind motion. So it can continually update the heading to archive good wing efficiency.

## Zigzag algorithm

The zigzag algorithm is very simple. When inside the track, the zone is free for zigzag to decide where to head.

We first use the current wing angle to see if it is in the no sail zone. Then compare it to the course to target waypoint. If we will turn into the no sail zone, then we cancel the angle out so the boat follows the edge of the zone instead. It will continue to sail this until it reaches the other side track border, where it will reconsider which zone edge to follow.



## Code implementation

Please refer to the [firmware repo](https://github.com/majianjia/DeepPlankter-firmware) or the [simulator repo](https://github.com/majianjia/nav-sim) for the implementation. 

## Simulation in extreme situation

Finally this is the simulation in frequent changed wind direction. 

- added 20deg P-P wind direction noise (every cycle)

See the top-right corner arrow which indicates the average wind direction (the actual change of wind direction is much quicker). See also the "wing effi" statistics on the right-hand list, which records the percentage of time that when the wing is outside of "no-sail" zone (means the wings is effectively providing propulsion). The route that boat is changing very frequently to allow the wing in high-efficiency angles. Sometimes it even sails the boat backward.



Overall, this navigation method can drive the boat to the destination even in an extreme scenario.

You can run the simulator yourself by downloading the code from the  [simulator repo](https://github.com/majianjia/nav-sim). The environment can be changed through the source code.

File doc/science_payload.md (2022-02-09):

# Science Payload

What is science payload and how does it implemented. 

## Data and On-board Processing

When the boat is in the middle of an ocean, the communication ability will be very limited. Normally, only heart-beat package and status data will be transferred back to us in "real-time".  All raw sensor data will be stored into the on board memory. If we are lucky enough, the boat can safely sail back to us,  we then can retrieve these valuable data.

Due to the limitation of memory, most of the data will be record at a lower data rate (1Hz), but some sensors might have a real sampling rate of 20Hz or higher. Which means a huge loss of data if we only analysis the recorded data. 

Also, some data is more valuable in real-time than post processing, such as weather or water data. These data is preferable to be processed and send back to us in real-time rather than being post processing months later.  

Therefore, for some application, data processing is better to perform onboard. 

- data processing that needs high rate sensor data, such as motion data
- data processing results that needs to send back in "real-time".

For example, we can use the high rate motion data to calculate the wave-height, then send the result back to us every hour. The data processing results is only a few bytes which is small enough to be packed into the heart-beat message.  

## Virtual Machine and Small Program

Science payload are a small programs that can run on the main MCU through a Virtual Machine (VM). 

Using an independent VM has some benefits.

- programs can be loaded from file system so it is exchangeable. 
- can be upgraded over-the-air. 
- split working environments, therefore protect the controller functions from the user program.  
- can also be used to overwrite controller's native functions such as navigation. 

There are some trade-off when using VM. VM are always slower compared to native and the runtime normally takes a great amount of resources (especially with RAM). Since the MCU is quite powerful and it has a large 1MB RAM, it is not a problem to run an embedded VM with some small programs. 

I compared a few different VM, such as micropython, lua, and a few wasm engines, also the rt-thread's own dynamic module. The final choose is [WASM-Micro-Runtime (wamr)](https://github.com/bytecodealliance/wasm-micro-runtime). It has some clear advantages. 

- It has ahead of time (AoT) compiling. Can achieve 0.7 ~0.9x native code speed. 
- It is small enough. Support both Interpreter mode or AoT mode. 
- Binary is small enough so that can be transfer even with satellites communication. 
- It has memory boundary checking. 
- User side programing is very easy, it is basically a WebAssembly program that can be written by any supported language, rust, C, C++..

# Setup Development Environment

The user side is very easy. Just download the [wasi-sdk](https://github.com/WebAssembly/wasi-sdk/releases) and set up according to its tutorial.

A simple program compiled by default config is enough, which is a normal webassembly application with bytecode for interpreter-based interpreter. You could put it to online site to run already. Most importantly, our boat controller is already capable to run this. 

The program takes around 29kB by default compiling option. 

However, this program will be quite large and slow. We can follow the wamr's suggest options to optimize the code. 

```
/opt/wasi-sdk/bin/clang -O3 -nostdlib \
    -z stack-size=8192 -Wl,--initial-memory=65536 \
    -o test.wasm test.c \
    -Wl,--export=main -Wl,--export=__main_argc_argv \
    -Wl,--export=__heap_base -Wl,--export=__data_end \
    -Wl,--no-entry -Wl,--strip-all -Wl,--allow-undefined
```

Finally, we can further use  wamr's tools and follow [the tutorial](https://github.com/bytecodealliance/wasm-micro-runtime/blob/main/doc/build_wasm_app.md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) to translate the interpreter-based bytecode to platform native bytecode to achieve native level speed. 

# App Framework

For science payloads, it is treated as an simple App. To be notice that the this App framework is not the App Framework in wamr. 

There are 3 methods for each App. 

```c
init() {};
epoch() {};
uninit() {};
```

- `init()` will be called when the system start up, where the app should resume the state when needed. Normally after a day reset. 

- `epoch()`will be called at every period to do the majority of the works. (Setting such as period, heap size, etc. will be set through related parameters).  

- `uinit()` will be called before the system reset. It is where the app should store the current state if needed.  

Each App has it own set of parameters, can be used to keep the state or communicate to the remote. User app can also simply use global variable to stored data and state across different epoch call.   

App can access filesystem when required, but should be limited to loading or writing configuration files. Instead, for data recording, the system has provided an async recorder interfaces, managed by an independent thread and the memory is in system space. It will queue the data, automatically split the file when the size is too large, and flush data into the filesystem every a few seconds. It is much safer to use the recorder interface for recording than accessing filesystem from App.  

# Example

 Run an hello world in .

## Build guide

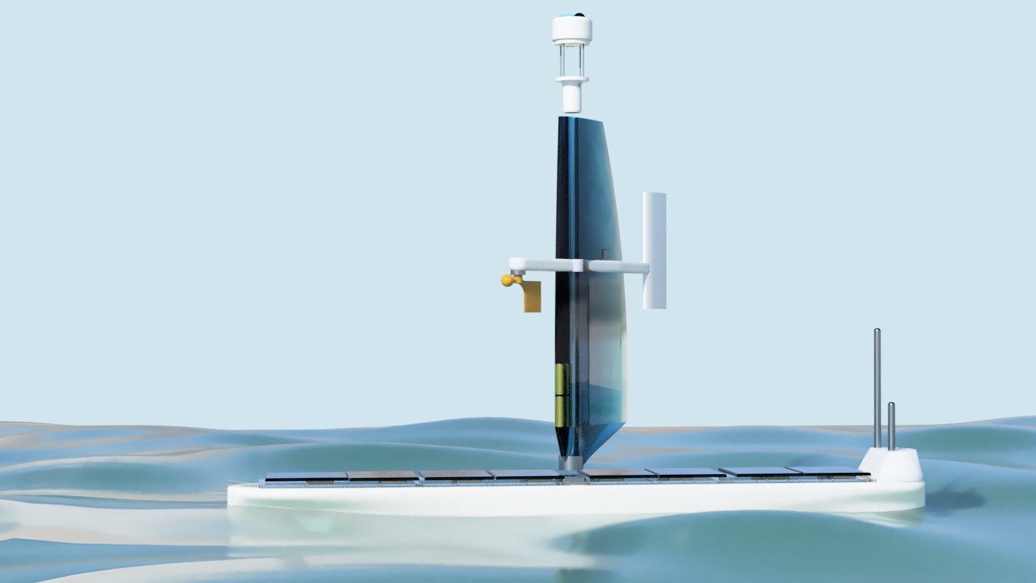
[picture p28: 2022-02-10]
doc/figures/dp_assembly_render_7.PNG

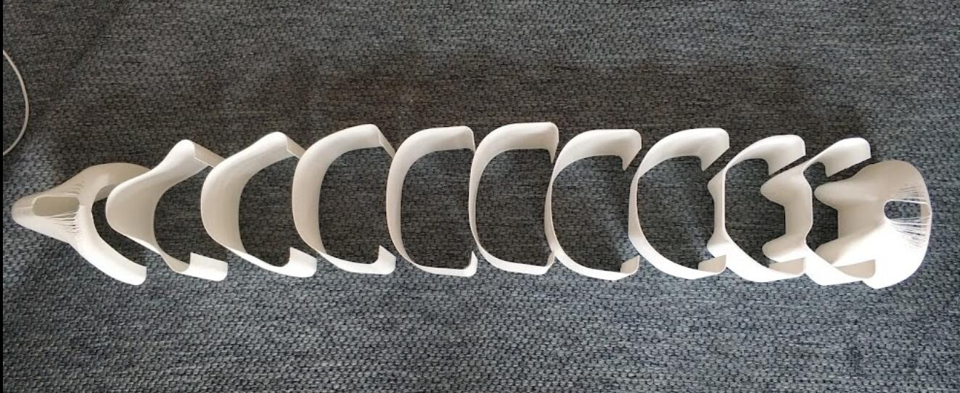
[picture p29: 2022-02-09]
doc/figures/hull_printed_all_section.jpg

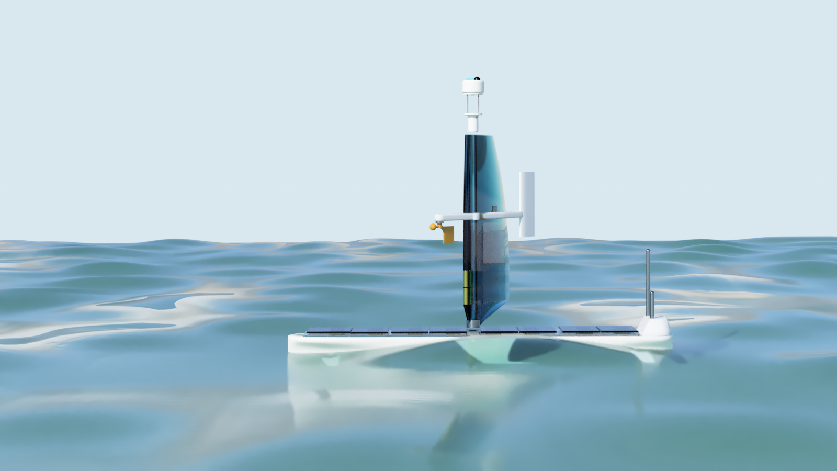
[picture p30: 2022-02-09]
doc/figures/dp_assembly_render_4.PNG

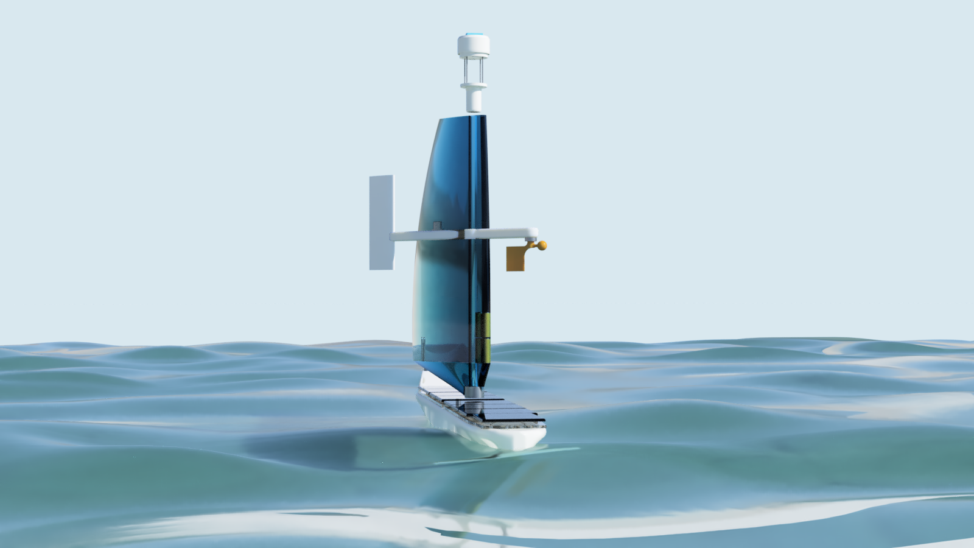
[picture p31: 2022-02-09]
doc/figures/dp_assembly_render_5.PNG

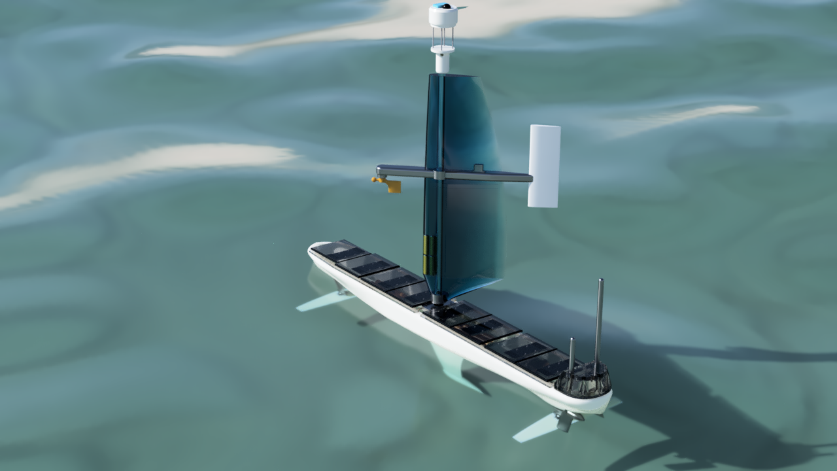
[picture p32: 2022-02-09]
doc/figures/dp_assembly_render_2.PNG

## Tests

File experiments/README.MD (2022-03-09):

# CAUTION

Files (including photos) in this folder should **NOT** be used in anywhere or publication without written permission from the author, i.e. Jianjia Ma.

For permission, please contact me using the [contact](../README.md#contact) at the bottom of the main repo page.

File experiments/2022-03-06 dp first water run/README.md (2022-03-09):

See [the main log here](../../doc/exp1_pond.md) for the detail of this experiment.

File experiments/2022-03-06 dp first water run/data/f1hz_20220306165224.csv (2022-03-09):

timestamp | cpu_load | sys_ram | sys_sd | sys_volt | sys_curr | sys_pwr | sys_vbat | mcu_temp | gyro_temp | bat_v0 | bat_i0 | bat_ich0 | bat_t0 | bat_soc0 | bat_v1 | bat_i1 | bat_ich1 | bat_t1 | bat_soc1 | esc_i | serv_i1 | serv_i2 | eular_x | eular_y | eular_z | pressure | humidity | air_temp | servo1_ang | servo2_ang | esc_thr | gnss_lat | gnss_lon | gnss_speed | gnss_alt | gnss_course | gnss_sat
1646585545 | 0.00 | 0.000 | 0.000 | 2.496 | 0.1017 | 0.8177 | 2.9675 | 24.3 | 19.250 | 8.0159 | -0.0652 | 0.0006 | 0.0000 | 0.0000 | 7.9534 | -0.0357 | 0.0005 | 0.0000 | 0.0000 | -0.0018 | 0.0384 | 0.0139 | 4.57 | -2.54 | -50.04 | 102359.55 | 35.14 | 22.042 | 0.0 | 0.0 | 0 | 0.000000 | 0.000000 | 0.00 | nan | 0.0 | 0
1646585546 | 0.00 | 0.000 | 0.000 | 2.500 | 0.1075 | 0.8647 | 3.0742 | 24.2 | 19.375 | 8.0340 | -0.0673 | -0.0001 | 0.0000 | 0.0000 | 7.9692 | -0.0393 | 0.0014 | 0.0000 | 0.0000 | -0.0004 | 0.0259 | 0.0149 | 5.54 | -2.38 | -57.68 | 102357.95 | 35.01 | 22.020 | 0.0 | 0.0 | 0 | 0.000000 | 0.000000 | 0.00 | nan | 0.0 | 0
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

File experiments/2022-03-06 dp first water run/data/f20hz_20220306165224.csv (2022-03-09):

timestamp | acc_x | acc_y | acc_z | gyro_x | gyro_y | gyro_z | mag_x | mag_y | mag_z | gyro_temp | eular_x | eular_y | eular_z | quat_q0 | quat_q1 | quat_q2 | quat_q3 | pressure
1646585544 | -0.0542 | 0.0872 | 0.9817 | -4.0894 | -0.0610 | 1.4648 | -0.0211 | 0.0656 | -0.4201 | 19.250 | 3.59 | -2.17 | -45.03 | 0.9218255 | 0.0216894 | -0.0295076 | -0.3814810 | 102363.77
1646585544 | -0.0366 | 0.0923 | 0.9897 | 0.7324 | 0.2441 | 0.6104 | -0.0229 | 0.0683 | -0.4192 | 19.250 | 3.60 | -2.39 | -45.43 | 0.9205350 | 0.0209611 | -0.0313792 | -0.3845779 | 102364.75
1646585545 | -0.0352 | 0.1018 | 0.9897 | 0.0610 | -0.0610 | 0.4883 | -0.0266 | 0.0665 | -0.4201 | 19.250 | 3.81 | -2.57 | -45.81 | 0.9191920 | 0.0219022 | -0.0336499 | -0.3875358 | 102360.02
1646585545 | -0.0388 | 0.0960 | 0.9853 | -0.0610 | 0.0610 | 0.2441 | -0.0248 | 0.0647 | -0.4201 | 19.250 | 3.82 | -2.49 | -46.26 | 0.9176843 | 0.0221918 | -0.0331178 | -0.3911501 | 102360.68
1646585545 | -0.0396 | 0.1011 | 0.9912 | 0.2441 | -0.1831 | 0.3052 | -0.0275 | 0.0612 | -0.4238 | 19.250 | 4.02 | -2.45 | -46.68 | 0.9161815 | 0.0237507 | -0.0335577 | -0.3945217 | 102362.78
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

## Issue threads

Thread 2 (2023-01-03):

Continuing the project.

felixJ86, 2023-01-03:
Hi as you may have notice i have made a fork of this project. and this is because i would like to continue this project. and if possible would like to get my hands on the source code as well. is this ok with you?

majianjia, 2023-01-04:
Yes I am fine, thank you! Thanks for your interest.
Please refer to https://github.com/majianjia/DeepPlankter/issues/1#issuecomment-1369482837 for the current status of this project.
There is still some security info that needs to be cleaned before it can be released, never have a chance to do it.
I will check today.

felixJ86, 2023-01-04:
ok thank you.

Closed 2023-01-04.

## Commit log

2021-02-18 Initial summit
    [Connector.SchDoc, DeepPlankter_main.PrjPcb, aux_powers.SchDoc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]
2022-02-09 Hull build log
2022-02-17 under water wing doc
2022-03-09 Add first experiment.
    [f1hz_20220306165224.csv, f20hz_20220306165224.csv]
2022-03-25 power plan explain
